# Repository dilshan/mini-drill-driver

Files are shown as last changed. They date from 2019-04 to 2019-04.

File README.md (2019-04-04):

# Replacement motor driver for INGCO mini drills

This is replacement motor driver for [INGCO](http://ingcotools.com) mini drills / die grinders. This project is mainly developed to replace motor speed controller of the *INGCO  MG1502.2* mini drill. 

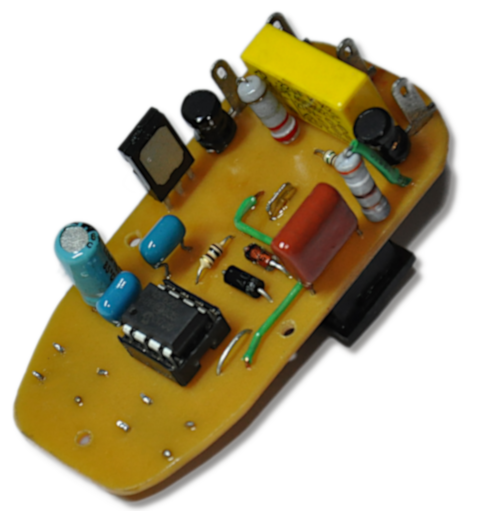
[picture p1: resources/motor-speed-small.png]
PCB of mini drill controller


This speed controller is designed based on Microchip [PIC12F629](https://www.microchip.com/wwwproducts/en/PIC12F629) 8-bit CMOS microcontroller.  This MCU is used for zero-crossing detection, determine TRIAC firing times and to handle buttons and switches.

As an original board, the controller supply comes from the mains through a simple RCD circuit. 

The firmware of this controller is design to operate with 4MHz internal-oscillator of the MCU. The current version of this controller is designed to work with 50Hz AC power sources. For 60Hz, *TIMER0* timing value needs to be changed in the firmware source code. 

Compare with the original *MG1502.2* controller board this controller is not equipped with LCD. We remove LCD from this design due to the unavailability of compatibaly LCD modules. Also, we design this controller using commonly available through-hole type components.  

**WARNING:** This controller board is powered by AC mains voltage. Avoid touching the board when power is applied. If possible, use an isolation transformer for the testing.

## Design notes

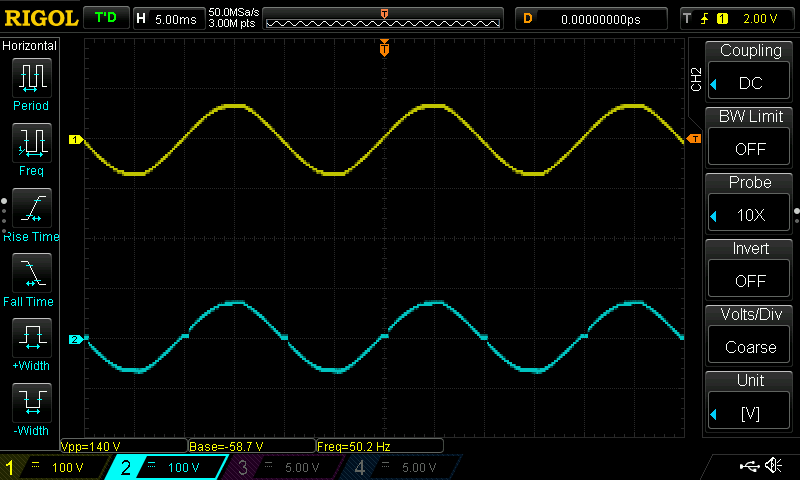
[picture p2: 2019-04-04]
resources/high-speed-triac-waveform.png

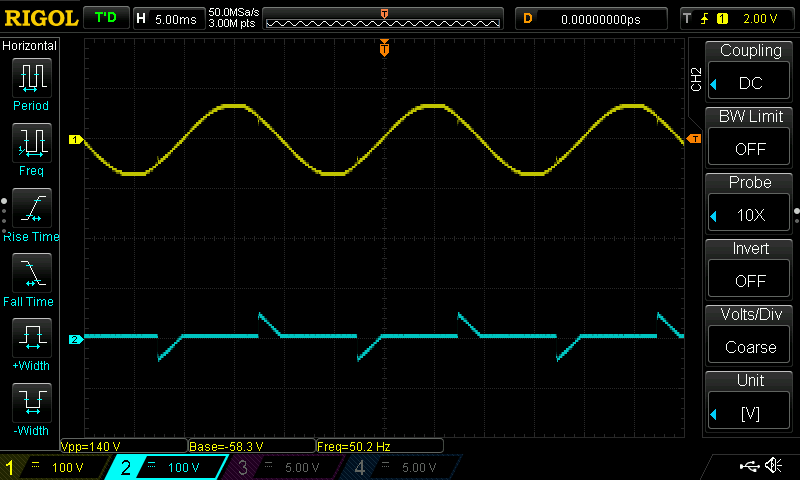
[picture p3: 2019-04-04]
resources/low-speed-triac-waveform.png

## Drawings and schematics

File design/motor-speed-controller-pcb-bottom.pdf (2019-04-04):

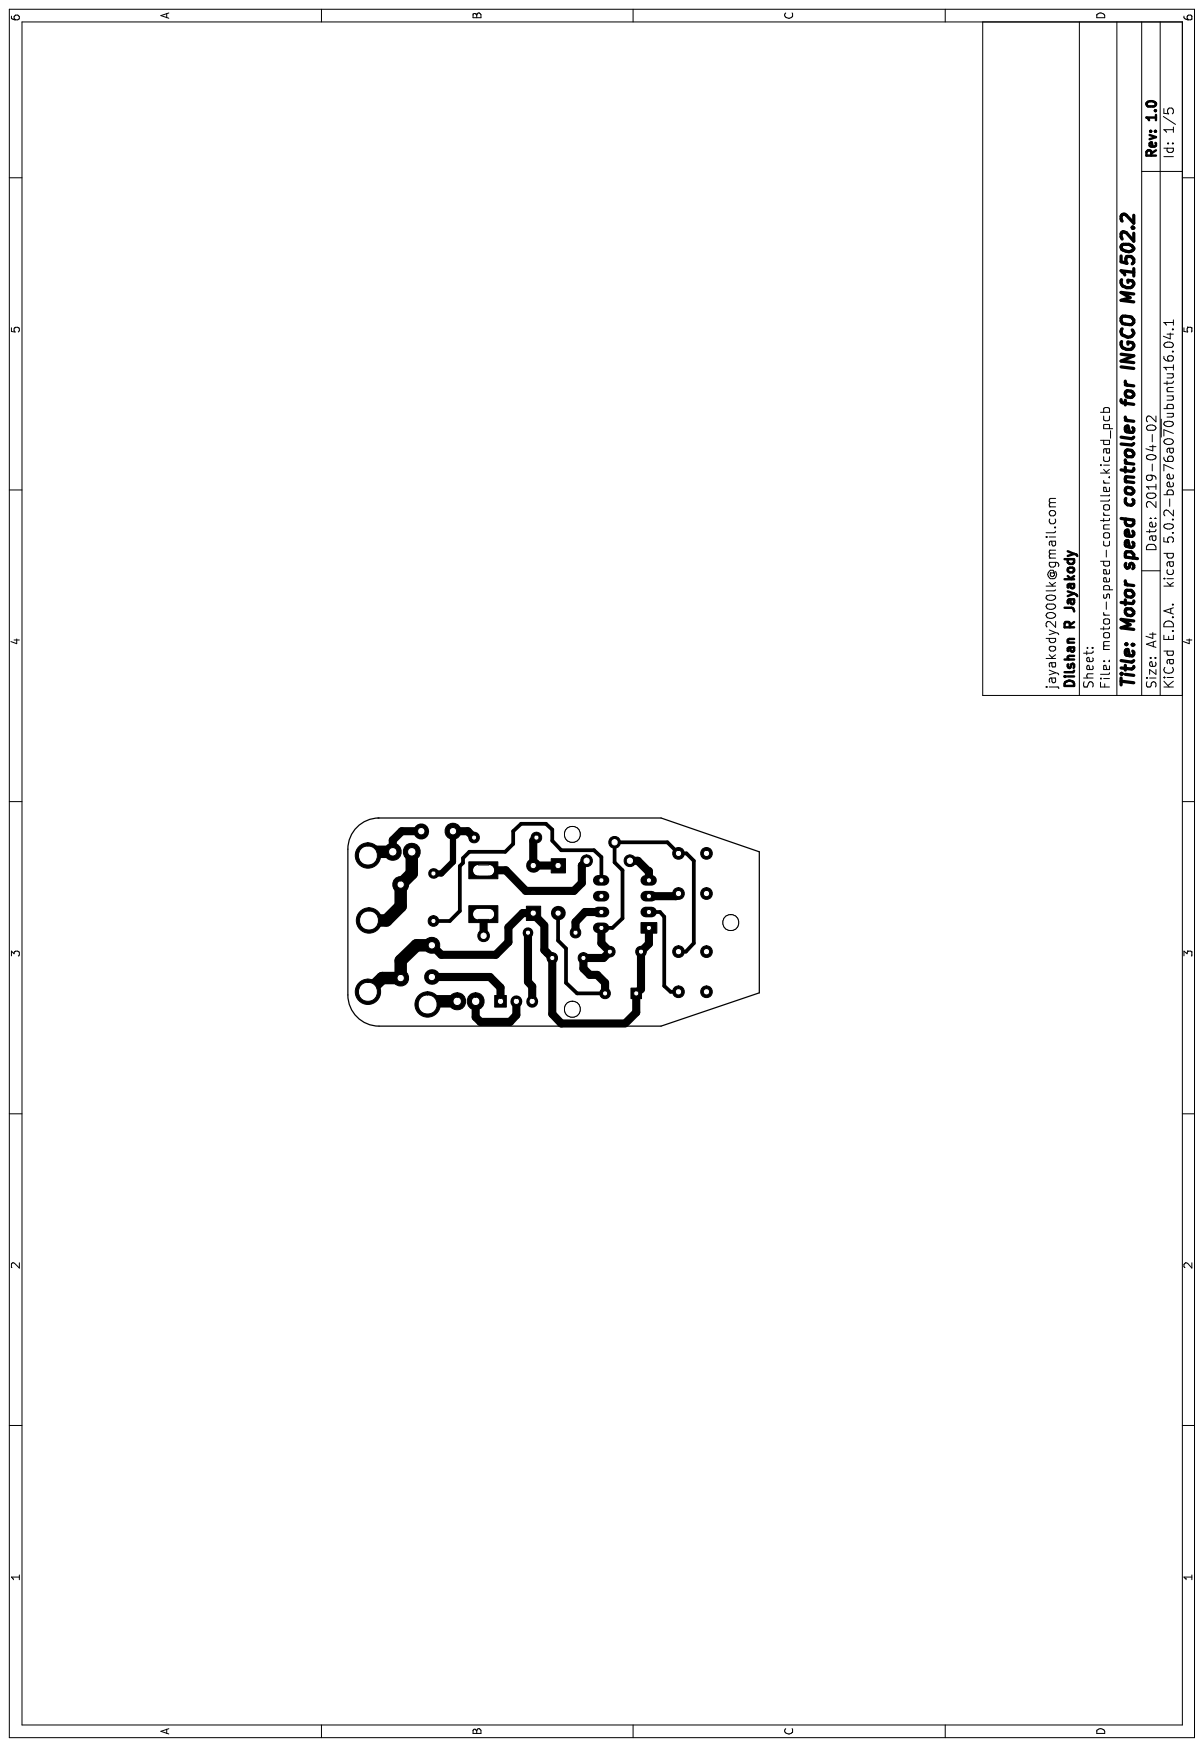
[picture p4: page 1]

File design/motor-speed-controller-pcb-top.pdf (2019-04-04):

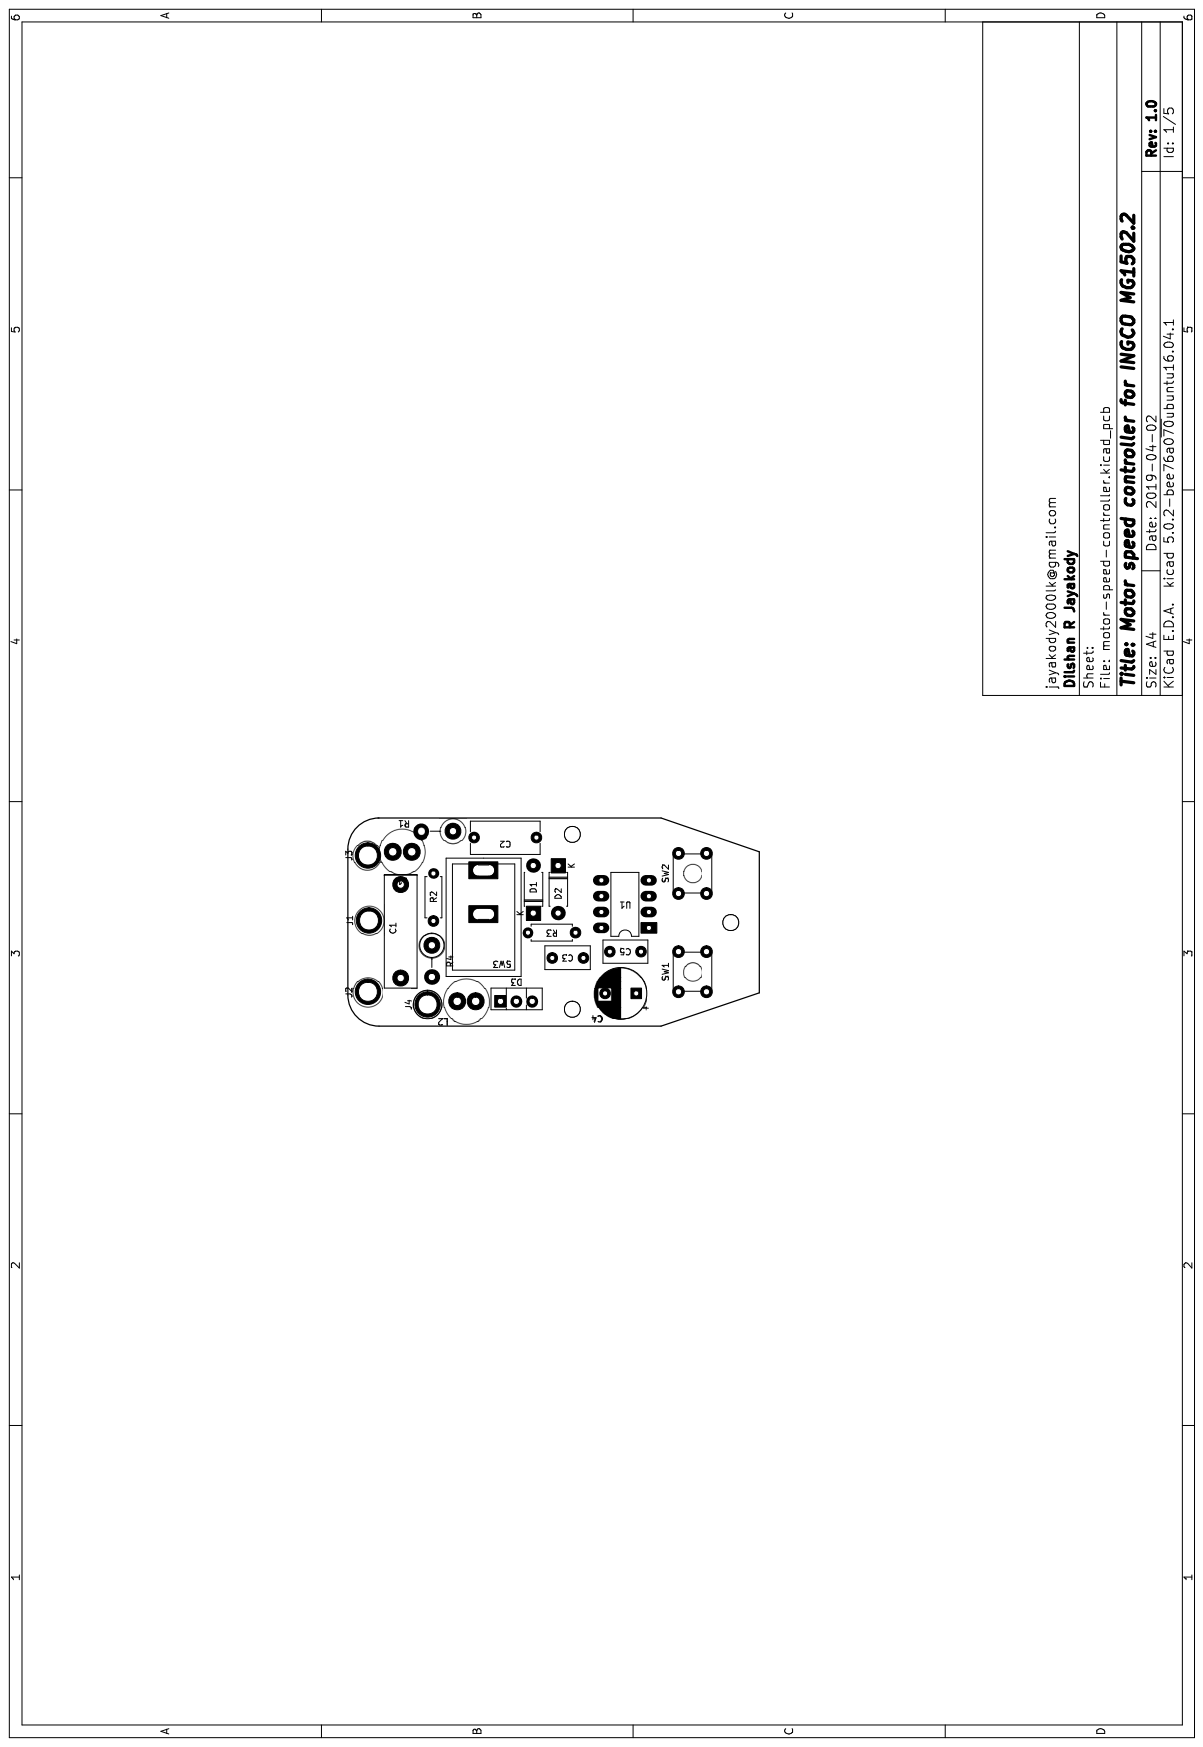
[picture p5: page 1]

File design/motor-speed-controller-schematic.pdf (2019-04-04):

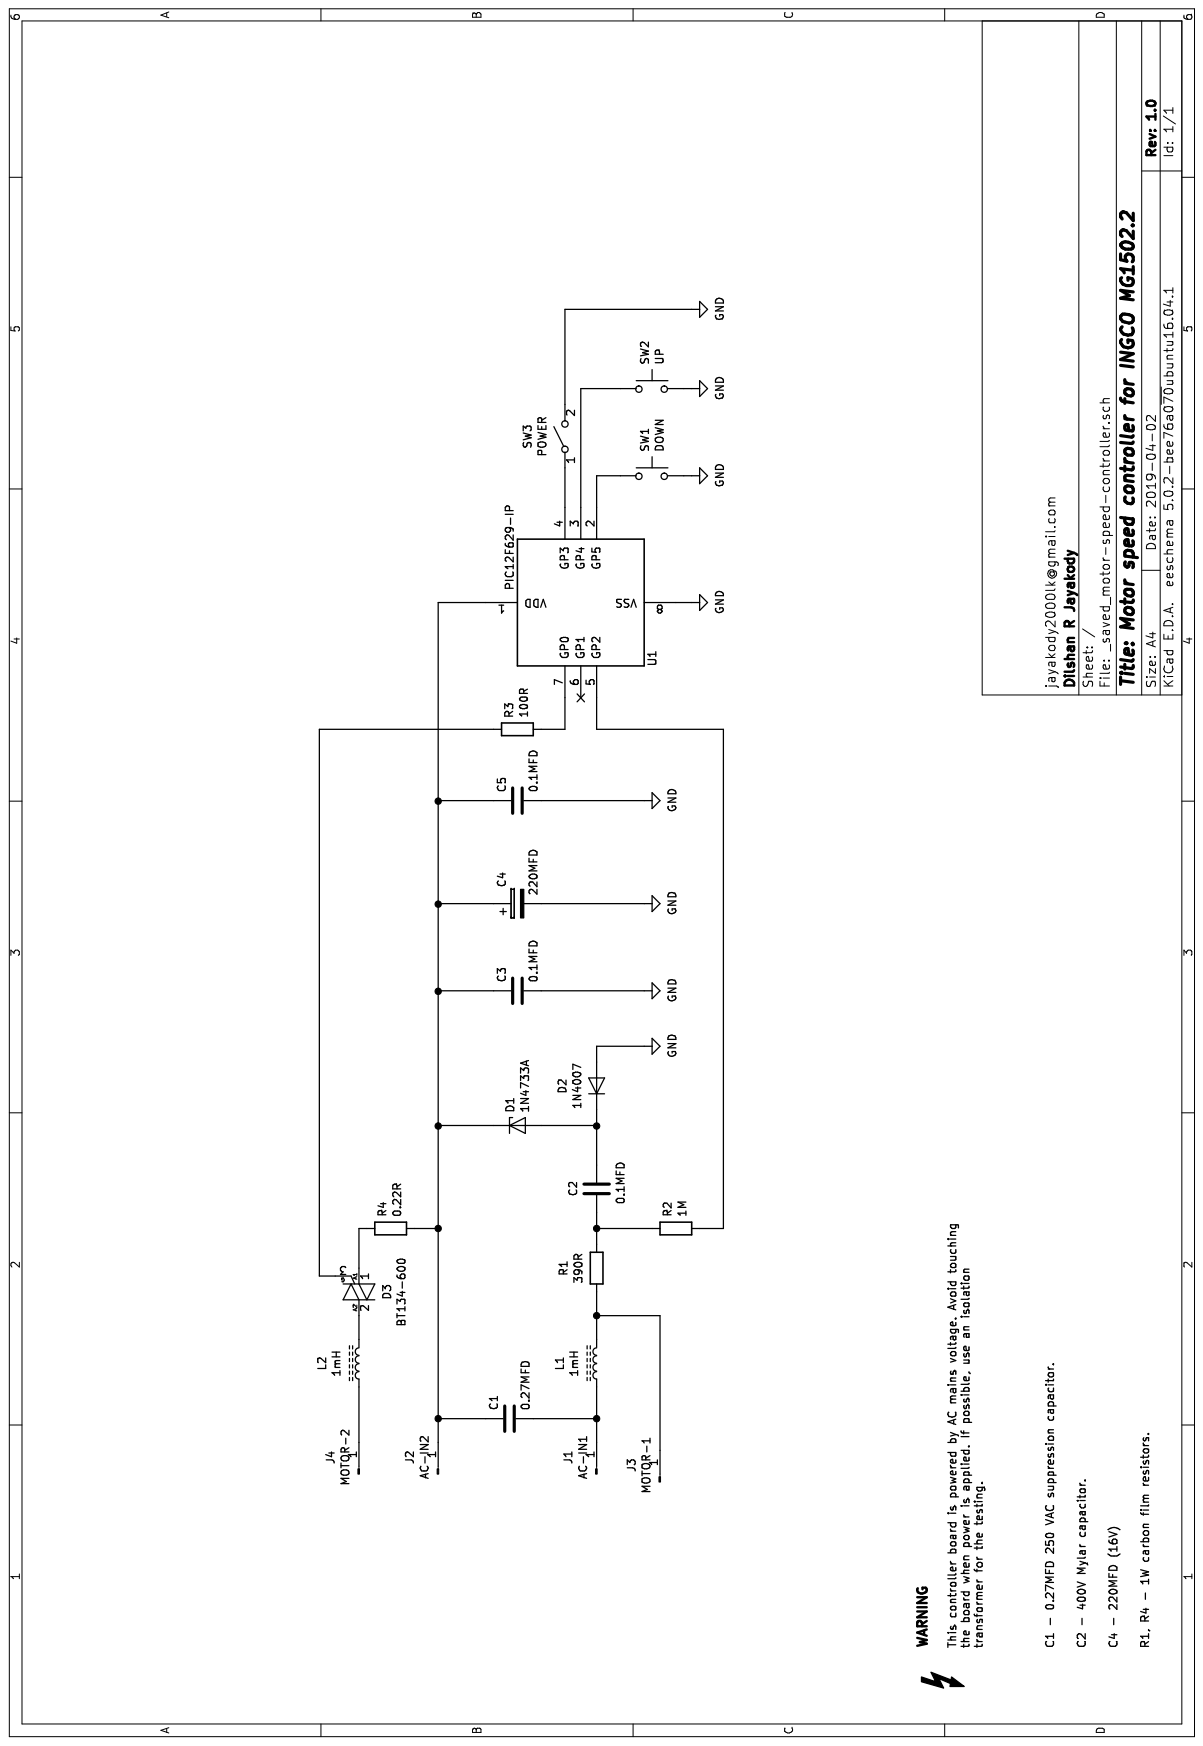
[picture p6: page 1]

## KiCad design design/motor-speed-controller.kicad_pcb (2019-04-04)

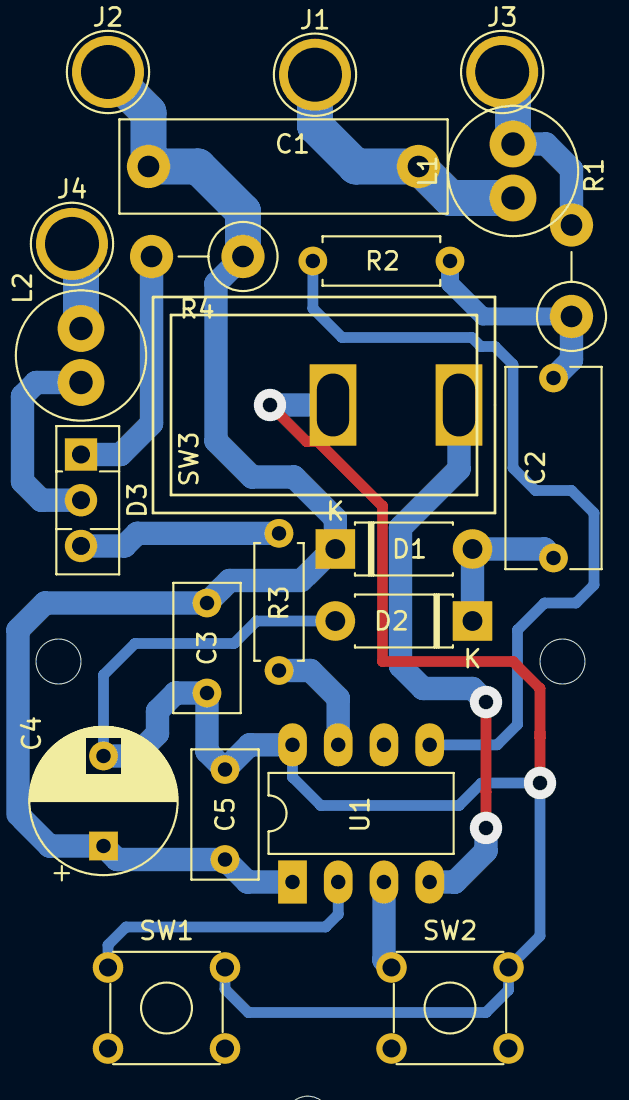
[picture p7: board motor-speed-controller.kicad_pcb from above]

Board: 2 copper layers, 25 parts (0 on the bottom side), 15 nets.

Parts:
C1: 0.27MFD; C_Rect_L18.0mm_W5.0mm_P15.00mm_FKS3_FKP3
C2: 0.1MFD; C_Rect_L11.0mm_W5.1mm_P10.00mm_MKT
C3, C5: 0.1MFD; C_Rect_L7.0mm_W3.5mm_P5.00mm
C4: 220MFD; CP_Radial_D8.0mm_P5.00mm
D1: 1N4733A; D_DO-41_SOD81_P7.62mm_Horizontal
D2: 1N4007; D_DO-41_SOD81_P7.62mm_Horizontal
D3: BT134-600; TO-126-3_Vertical
H1, H2, H3: MountingHole_2.5mm
J1, J2: AC-IN1; TestPoint_Plated_Hole_D3.0mm
J3: MOTOR-1; TestPoint_Plated_Hole_D3.0mm
J4: MOTOR-2; TestPoint_Plated_Hole_D3.0mm
L1, L2: 1mH; L_Radial_D7.0mm_P3.00mm
R1: 390R; R_Axial_DIN0411_L9.9mm_D3.6mm_P5.08mm_Vertical
R2: 1M; R_Axial_DIN0207_L6.3mm_D2.5mm_P7.62mm_Horizontal
R3: 100R; R_Axial_DIN0207_L6.3mm_D2.5mm_P7.62mm_Horizontal
R4: 0.22R; R_Axial_DIN0411_L9.9mm_D3.6mm_P5.08mm_Vertical
SW1: DOWN; SW_TH_Tactile_Omron_B3F-10xx
SW2: UP; SW_TH_Tactile_Omron_B3F-10xx
SW3: POWER; SWITCH-SPST
U1: PIC12F629-IP; DIP-8_W7.62mm_LongPads

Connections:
GND: C3.2, C4.2, C5.2, D2.2, SW1.2, SW2.2, SW3.2, U1.8
unnamed: C1.1, C3.1, C4.1, C5.1, D1.1, J2.1, R4.1, U1.1
unnamed: C1.2, J1.1, L1.1
unnamed: C2.1, D1.2, D2.1
unnamed: C2.2, R1.1, R2.2
unnamed: D3.1, R4.2
unnamed: D3.2, L2.2
unnamed: D3.3, R3.2
unnamed: J3.1, L1.2, R1.2
unnamed: J4.1, L2.1
unnamed: R2.1, U1.5
unnamed: R3.1, U1.7
unnamed: SW1.1, U1.2
unnamed: SW2.1, U1.3
unnamed: SW3.1, U1.4

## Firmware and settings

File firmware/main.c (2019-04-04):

/*******************************************************************************
 Copyright (c) 2019 Dilshan R Jayakody. [jayakody2000lk@gmail.com]

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
 THE SOFTWARE IS PROVIDED "AS IS", WITHOUT WARRANTY OF ANY KIND, EXPRESS OR 
 IMPLIED, INCLUDING BUT NOT LIMITED TO THE WARRANTIES OF MERCHANTABILITY, 
 FITNESS FOR A PARTICULAR PURPOSE AND NONINFRINGEMENT. IN NO EVENT SHALL THE 
 AUTHORS OR COPYRIGHT HOLDERS BE LIABLE FOR ANY CLAIM, DAMAGES OR OTHER
 LIABILITY, WHETHER IN AN ACTION OF CONTRACT, TORT OR OTHERWISE, ARISING FROM, 
 OUT OF OR IN CONNECTION WITH THE SOFTWARE OR THE USE OR OTHER DEALINGS IN THE 
 SOFTWARE.
 ******************************************************************************/

#include "main.h"

unsigned char timerPos = 0;

int main() 
{
    unsigned char portStatus = 0x03;
    unsigned char lastStatus = 0x03;
    unsigned char tempVal; 
    
    // Initialize system and load last Traic timing value from E2PROM.
    initSystem();
    __delay_ms(10);
    triggerTime = eeprom_read(0x00);
    
    // Clamp Traic timing value into valid range.
    if((triggerTime < MIN_TIME) || (triggerTime > MAX_TIME))
    {
        triggerTime = 100;
    }
    
    while(1)
    {
        portStatus = GPIO;
        
        // Handle INC button event.
        if(((portStatus & 0x10) == 0x10) && ((lastStatus & 0x10) == 0x00))
        {
            triggerTime = (triggerTime > 5 + MIN_TIME) ? (triggerTime - 5) : MIN_TIME;
            eeprom_write(0x00, triggerTime);
        }
        
        // Handle DEC button event.
        if(((portStatus & 0x20) == 0x20) && ((lastStatus & 0x20) == 0x00))
        {
            tempVal = triggerTime;
            tempVal += 5;
            
            if(tempVal >= MAX_TIME)
            {
                tempVal = MAX_TIME;
            }
            
            triggerTime = tempVal;
            eeprom_write(0x00, triggerTime);
        }
        
        lastStatus = portStatus;
        __delay_ms(10);
    }
    
    return 0;
}

void __interrupt () interruptHandler()
{
    // Check POWER button status.
    if((GPIO & 0x8) == 0x0)
    {
        // Edge interrupt handler to manage first 180 degrees of the wave.
        if((INTCON & 0x02) == 0x02)
        {
            // Timer 0 is set to handle 50Hz AC line.
				TMR0 = 90; 
            INTCON = 0xE0;

            for(timerPos = 0; timerPos < triggerTime; timerPos++)
            {
                __delay_us(50);
            }

            GPIO = 0x00;
            __delay_us(50);
            GPIO = 0x03;
        }

        // Timer0 interrupt handler to manage remaining 180 degrees of the wave. 
        if((INTCON & 0x04) == 0x04) 
        {
            NOP();
            NOP();

            for(timerPos = 0; timerPos < triggerTime; timerPos++)
            {
                __delay_us(50);
            }

            GPIO = 0x00;
            __delay_us(50);
            GPIO = 0x03;

            INTCON = 0xD0;
        }
    }
    else 
    {
        // POWER button is in OFF state and therefor ignore all interrupts.
        GPIO = 0x03;
        INTCON = 0xD0;
    }
}

void initSystem()
{
    triggerTime = 100;
    
    // Setup GPIO port of the PIC16F629 MCU.
    GPIO = 0x03;
    TRISIO = 0x3C;
    
    // Configure pull-up for GPIO port.
    OPTION_REG = 0x45;
    WPU = 0x38;

    // Disable comparator and enable interrupts.
    CMCON = 0x07;
    INTCON = 0xD0;
}
